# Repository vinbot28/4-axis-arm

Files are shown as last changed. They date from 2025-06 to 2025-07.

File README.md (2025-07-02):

# 4 Axis Arm
The **4 Axis Arm** is exactly what you think it is. Using 4 servos, the robotic arm achieves 4 degree of freedom movement through the: turret base, shoulder, elbow, and wrist rotation joints. All of the 3d printed parts are designed to use zero to no supports, and there are very few parts in the whole assembly. I've also created an electronics box containing potentiometers, an Arduino Nano (for its popularity and accessibility), and a custom PCB to greatly decrease the wiring hassle. 

Screenshot 2025-06-30 at 8 35 14 AM

Screenshot 2025-06-30 at 8 35 14 AM

Screenshot 2025-06-30 at 8 35 14 AM\
The wiring diagram for the potentiometers to PCB.

I created this project after seeing so many 6 axis arms pop up all over YouTube. Wanting one of my own, I quickly realized how much the components costed and the complexity of the control systems. Despite that, I really wanted to design and play with a robotic arm, and hence the decision to make a 4 axis. Additionally, I couldn't pass down the opportunity to CAD and design a PCB...

# General Instructions:
## Wiring: 
The PCB Silkscreen includes labels for which ports correspond to what component. Px = potentiometer; Sx = servo.\
Potentiometers:
- Pot 1      -> P1 (pcb) = Pin 19 (arduino)
- Pot 2      -> P2 (pcb) = Pin 20 (arduino) 
- Pot 3      -> P3 (pcb) = Pin 21 (arduino)
- Pot 4      -> P4 (pcb) = Pin 22 (arduino)
- Pot 5/claw -> P5 (pcb) = Pin 23 (arduino)

Servos:
- Servo 1/turret   -> S1 (pcb) = Pin 6 (arduino)
- Servo 2/shoulder -> S2 (pcb) = Pin 8 (arduino)
- Servo 3/elbow    -> S3 (pcb) = Pin 9 (arduino)
- Servo 4/wrist    -> S4 (pcb) = Pin 12 (arduino)
- Servo 5/effector -> S5 (pcb) = Pin 14 (arduino)

## Programming:
A sample program is included in this repository to control the servos using the potentiometers. Feel free to create your own programs to run pre-programmed movements, serial-based control, and much more!

# Bill of Materials:

| Item name | Amount Needed | Packs to buy | Total Cost | Link |
|---|---|---|---|---|
| MG946R Servo | 4 | 4 | 14.52 | https://www.aliexpress.us/item/3256806315358281.html |
| M4 6x5 Heat set | 23 | 1 | 2.64 | https://www.aliexpress.us/item/3256803396040989.html |
| M3 3x5 Heat set | 3 | 1 | 2.05 | https://www.aliexpress.us/item/3256803396040989.html |
| M4-6 SHCS | 20 | 1 | 1.55 | https://www.aliexpress.us/item/2255800598515019.html |
| M4-8 SHCS | 3 | 1 | 1.64 | https://www.aliexpress.us/item/2255800598515019.html |
| M3-6 SHCS | 3 | 1 | 1.41 | https://www.aliexpress.us/item/2255800598515019.html |
| Male/Female headers | 1 | 1 | 2.21 | https://www.aliexpress.us/item/2255800687544049.html |
| Female DC barrel jack | 1 | 1 | 1.53 | https://www.aliexpress.us/item/3256802343987191.html |
| Arduino nano | | 1 | 5.73 | https://www.aliexpress.us/item/3256806718205824.html |
| PCB | | 1 | 5 | jlcpcb.com |
| | | | | |
| 5v AC-DC Power supply | 1 | 1 | 9.99 | https://a.co/d/4vrQsQI |
| | | | | |
| | | Subtotal: | 48.27 | |
| | | Grand Total | 58.31 | |
| JLC Shipping | Aliexpress Shipping | Amazon Shipping | | |
| 3.2 | 6.84 | N/A | | |

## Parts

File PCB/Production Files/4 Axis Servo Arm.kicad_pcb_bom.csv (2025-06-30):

Designator | Quantity | Value | Footprint | Package | MPN | DNP | Mount_Type | Description
A1 | 1 | Arduino_Nano_v3.x | Arduino_Nano |  |  |  | tht | Arduino Nano v3.x
J1 | 1 | 5V DC BARREL | BarrelJack_Horizontal |  |  |  | tht | DC Barrel Jack with an internal switch
P1 | 1 | Pot_1 | PinHeader_1x03_P2.54mm_Vertical |  |  |  | tht | Generic connector, single row, 01x03, script generated (kicad-library-utils/schlib/autogen/connector/)
P2 | 1 | Pot_2 | PinHeader_1x03_P2.54mm_Vertical |  |  |  | tht | Generic connector, single row, 01x03, script generated (kicad-library-utils/schlib/autogen/connector/)
P3 | 1 | Pot_3 | PinHeader_1x03_P2.54mm_Vertical |  |  |  | tht | Generic connector, single row, 01x03, script generated (kicad-library-utils/schlib/autogen/connector/)
P4 | 1 | Pot_4 | PinHeader_1x03_P2.54mm_Vertical |  |  |  | tht | Generic connector, single row, 01x03, script generated (kicad-library-utils/schlib/autogen/connector/)
P5 | 1 | Pot_Claw | PinHeader_1x03_P2.54mm_Vertical |  |  |  | tht | Generic connector, single row, 01x03, script generated (kicad-library-utils/schlib/autogen/connector/)
S1 | 1 | Axis 1 | PinHeader_1x03_P2.54mm_Vertical |  |  |  | tht | Generic connector, single row, 01x03, script generated (kicad-library-utils/schlib/autogen/connector/)
S2 | 1 | Axis 2 | PinHeader_1x03_P2.54mm_Vertical |  |  |  | tht | Generic connector, single row, 01x03, script generated (kicad-library-utils/schlib/autogen/connector/)
S3 | 1 | Axis 3 | PinHeader_1x03_P2.54mm_Vertical |  |  |  | tht | Generic connector, single row, 01x03, script generated (kicad-library-utils/schlib/autogen/connector/)
S4 | 1 | Axis 4 | PinHeader_1x03_P2.54mm_Vertical |  |  |  | tht | Generic connector, single row, 01x03, script generated (kicad-library-utils/schlib/autogen/connector/)
S5 | 1 | Claw | PinHeader_1x03_P2.54mm_Vertical |  |  |  | tht | Generic connector, single row, 01x03, script generated (kicad-library-utils/schlib/autogen/connector/)

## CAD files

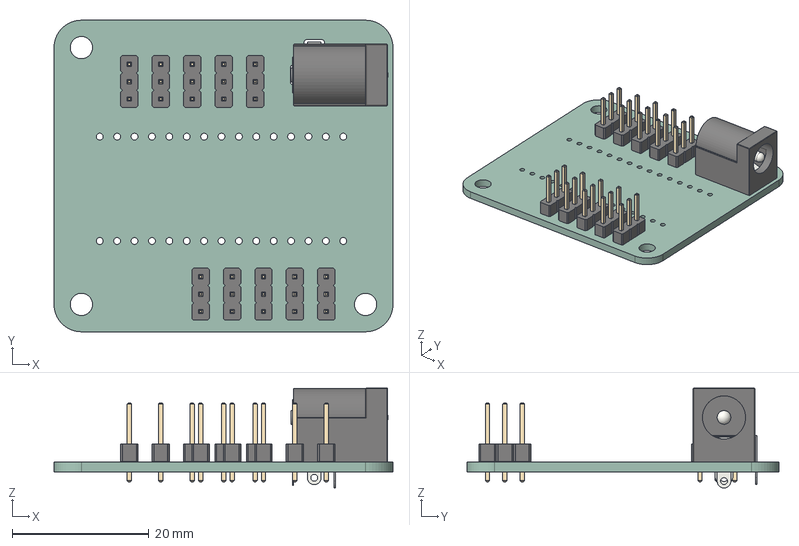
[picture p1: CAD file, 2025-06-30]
PCB/KiCad Files/4 Axis Servo Arm.step
49.5 x 45.5 x 14.6 mm
PinHeader_1x03_P2.54mm_Vertical x 10
BarrelJack_Horizontal
4 Axis Servo Arm_PCB

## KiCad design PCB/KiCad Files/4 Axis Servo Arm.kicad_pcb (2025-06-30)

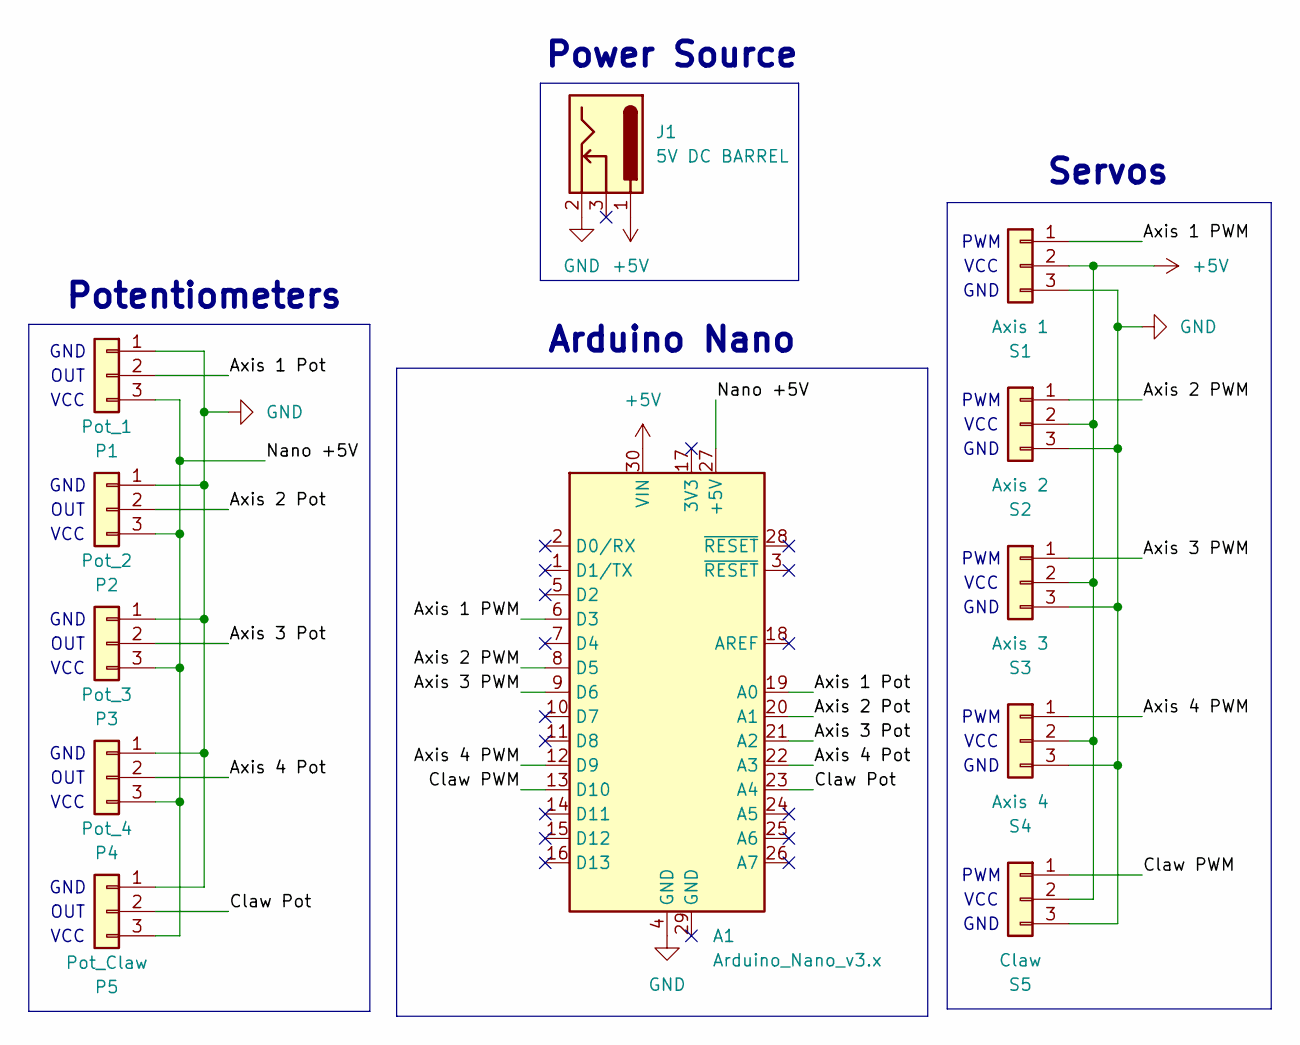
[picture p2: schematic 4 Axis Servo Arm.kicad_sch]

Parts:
A1: Arduino_Nano_v3.x; Arduino_Nano
J1: 5V DC BARREL; BarrelJack_Horizontal
P1: Pot_1; PinHeader_1x03_P2.54mm_Vertical
P2: Pot_2; PinHeader_1x03_P2.54mm_Vertical
P3: Pot_3; PinHeader_1x03_P2.54mm_Vertical
P4: Pot_4; PinHeader_1x03_P2.54mm_Vertical
P5: Pot_Claw; PinHeader_1x03_P2.54mm_Vertical
S1: Axis 1; PinHeader_1x03_P2.54mm_Vertical
S2: Axis 2; PinHeader_1x03_P2.54mm_Vertical
S3: Axis 3; PinHeader_1x03_P2.54mm_Vertical
S4: Axis 4; PinHeader_1x03_P2.54mm_Vertical
S5: Claw; PinHeader_1x03_P2.54mm_Vertical

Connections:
+5V: A1.30 (VIN), J1.1, S1.2, S2.2, S3.2, S4.2, S5.2
/Axis 1 PWM: A1.6 (D3), S1.1
/Axis 1 Pot: A1.19 (A0), P1.2
/Axis 2 PWM: A1.8 (D5), S2.1
/Axis 2 Pot: A1.20 (A1), P2.2
/Axis 3 PWM: A1.9 (D6), S3.1
/Axis 3 Pot: A1.21 (A2), P3.2
/Axis 4 PWM: A1.12 (D9), S4.1
/Axis 4 Pot: A1.22 (A3), P4.2
/Claw PWM: A1.13 (D10), S5.1
/Claw Pot: A1.23 (A4), P5.2
/Nano +5V: A1.27 (+5V), P1.3, P2.3, P3.3, P4.3, P5.3
GND: A1.4 (GND), J1.2, P1.1, P2.1, P3.1, P4.1, P5.1, S1.3, S2.3, S3.3, S4.3, S5.3

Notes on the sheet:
GND
PWM
VCC
GND
Servos
Potentiometers
Power Source
OUT
Arduino Nano

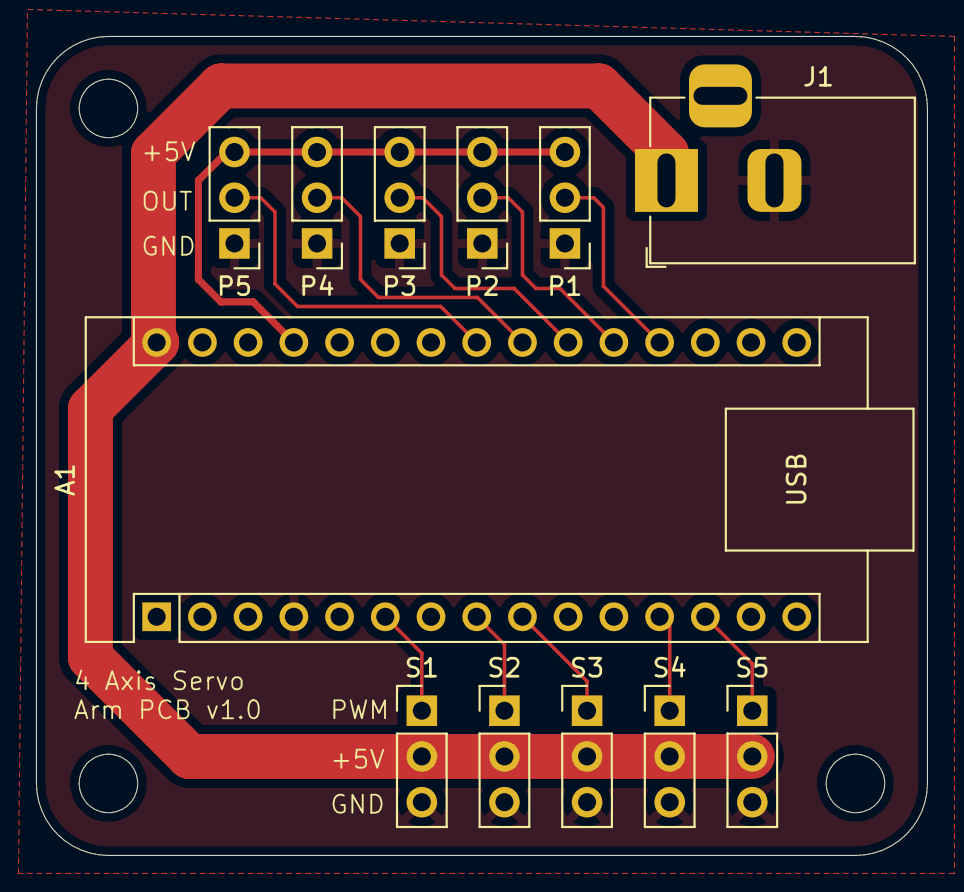
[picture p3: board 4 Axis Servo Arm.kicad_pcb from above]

Board: 2 copper layers, 49.5 x 45.5 mm, 12 parts (0 on the bottom side), 13 nets.

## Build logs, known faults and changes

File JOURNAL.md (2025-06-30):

---
title: 4 Axis Arm
author: Vincent
description: A robotic arm driven by servos and an Arduino.
created_at: 2025-06-18
---
## ***16.5 Total Hours***

# June 18th: Figured out the layout of the arm + got the base sorted out

Started cad work of the 4 axis. Also decided on using MG946R servos for their torque.

Axes: 
1. turret base
2. shoulder
3. elbow
4. wrist roll

CHALLENGE for this project: design all the 3d printed parts to not require slicer generated supports
* quite tedious to remove and it'd be a cool skill to have, especially since I do robotics and use 3d printing a lot

Single part base, printed upside down. Servo slots in from the bottom, and screws into some heat set inserts 
Assembly 2

Whole part is printed upside down, not requiring supports. To tackle the base mounting point overhangs, I added small bridges under to the counterbore. Much easier to understand in the photo, but it lets the printer have some material to print on top off.
I also chamfered the overhanging protrusion of the "legs" since printers don't struggle with printing at 45 degrees.
Assembly 2 (1)
Assembly 2 (2)

I'm currently doubting whether or not my servo cad file is correct in its dimensions, though it shouldn't be too bad to adjust them when I get the arm fabricated.

**Session Time: 3h**

# June 20: Shoulder axis (Axis 2)

Spent 30 minutes trying to decide how to continue the turret top without making it look so ugly. 
Settled on making the turret platform diameter from 90mm to 74mm. Also, chopping off unnecessary volume. Unfortunately, without splitting the part into two pieces, supports are needed for the shoulder servo recess. Maybe adjusting the goal to use supports only if they're fast and easy to remove?

Actually no I will just remove the bridged material since it's a waste of filament and space. Might also cause clearance issues when the arm is added later on:

Screenshot 2025-06-20 at 6 21 20 PM

I'm not going to lie, this (lack of) housing around the servo doesn't look too good. Thinking of having a cover plate but I don't want to increase complexity...\
Screenshot 2025-06-20 at 7 29 39 PM

Progress after ~2h of messing around:\
Axes 1 and 2 are completed! I added hardware models too, to make stuff look better. Moving on to designing the arm.\
Screenshot 2025-06-20 at 7 27 07 PM

Almost forget these cutouts for the servo mounting tabs.\
Screenshot 2025-06-20 at 9 55 33 PM

No clue how to make things look nice...it seems I can only tell if something's off. Especially in the case of the arm shape design.\
Screenshot 2025-06-20 at 8 07 26 PM

Made the arm shape look a bit nicer, + the 3rd axis servo mounting, but the arm looks too 2d.\
Screenshot 2025-06-20 at 10 23 25 PM

New issue: everything seems so skewed to the left, but my sketch for the turret base has so many lines that I can't tell what to change. Trying to move the shoulder servo closer to the center. Got it fixed though (second image). Everything is more centered and the forearm won't be too far from the center.\
Unfortunately, to stop the shoulder joint from being too cantilevered, I had to inset the surface where the shoulder servo horn connected to the arm. Hopefully supports are fine there.\
Screenshot 2025-06-20 at 11 18 13 PM
Screenshot 2025-06-20 at 11 24 43 PM

Attempted to beautify the arm. There's not much I can do to make it look nice besides spam chamfers and fillets, so that's what I did. Personally I think it looks pretty good, but it definitely still looks out of place. Good enough?
Screenshot 2025-06-20 at 11 45 23 PM

For tomorrow, should probably clean this plate up. Looks out of place.
Screenshot 2025-06-20 at 11 42 56 PM

End of day progress: Pretty good, accomplished axes 2 and started 3.\
Screenshot 2025-06-20 at 11 47 08 PM

**Session Time: 4.5h**

# June 21: Axis 3

Starting axis 3. Sketch for side view of axis 3 + axis 4 servo.\
Screenshot 2025-06-21 at 10 21 36 AM

Drew this up for the shape of the remaining axes:\
Screenshot 2025-06-21 at 10 24 27 AM

Finally something presentable for axis 3. Axis 4 will be inline with axis 3 point of rotation, and that defined many of the locational dimensions in the sketch. Also tried to include some curves so everything doesn't look to boring and simplistic.\
Screenshot 2025-06-21 at 12 00 22 PM

YES! No clearance issues today, and the proportions seem about right. Time to make the actual servo mount part.\
Screenshot 2025-06-21 at 12 07 20 PM

Finished servo mount. I'm not too sure if the actual mounting towers would break. With the (non) loads this arm will tackle, I have my doubts they'll break. It's also a 9.9mm^2 tower so I could just increase walls + infill as needed.\
Screenshot 2025-06-21 at 1 15 51 PM

I also took some time to recenter everything so that axis 4 is on the line of symmetry of the base:\
Screenshot 2025-06-21 at 1 19 06 PM
Screenshot 2025-06-21 at 1 19 16 PM

**Session Time. 2.5h**

# June 22: PCB TIME

Spent an hour trying to figure out what symbols and footprints to use for my components...and they're not even ICs. Had to watch some pcb tutorial videos to figure out what to use for 3 pin headers and the barrel jack. Attempted to connect the parts on the schematic, but it got messy quick.\


Learned of "labels?" which you can connect to and it bridges between connections to the same label. Made the schematic sooooo clean.\


I used the net checker tool to verify my connections went to the right spots. However, ERC gave me an error about output pins not going into input pins, or something like that. Some googling told me it's just a thing with the input/output power settings for the components. Also, I know that the connections are fine so I just ignored the error. MOVING ON TO PCB LAYOUT!!!

I organized the pin headers by servo or potentiometer, and put it on the respective sides of the nano where the connections didn't overlap each other. I may have redone the layout 3 times...anyway I learned to do a ground pour for the GND lines so I didn't have to route those traces. Yay! Thinking I was done, I ran the DRC, which gave me a "thermal relief connection to zone incomplete" error. Turns out my ground pour wasn't able to reach one of the ground pins on the nano. That was easy to fix just by moving my 5v line out of the way. And now, I have a PCB! I'll work on the silkscreen tomorrow.\



**Session Time. 3.5h**

# June 23

Finished the PCB. I added 3.25mm mounting holes, as well as some silkscreen labels. DRC checks were all good!\



Since the PCB was smooth sailing, I'm going to add an enclosure to this pcb. There needs to be something holding the potentiometers and protecting the board. Exported pcb as a .step from kicad.
Successfully imported it into onshape. I also added a nano model:\


Ended the day with figuring out the layout for the potentiometers and started the frame model. Going to use m3 heat sets to secure pcb, and m4 heat sets for the cover. 


**Session Time. 1.0h**

# June 29

Finished the electronics case. Adjusted the potentiometers to not block the servo ports. Good thing there's only 5 pots. 



I checked online for the usb and dc jack cable sizes, to make sure there's enough space for wire clearance:



Overall looks pretty good. Labeled the pots for the joints they would control. Seems like we're done!


** Session Time: 2.0h **

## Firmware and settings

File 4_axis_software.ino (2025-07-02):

#include <Servo.h>

// effector code has been commented out in case user wants to use expansion slot

// declaring servos
Servo turret;
Servo shoulder;
Servo elbow;
Servo wrist;
// Servo effector; 

// assigning pins to servos (pwm ports)
const int turretPin = 6;
const int shoulderPin = 8;
const int elbowPin = 9;
const int wristPin = 12;
// const int effectorPin = 14; 

// assigning pins to potentiometers (analog ports)
const int T_potPin = 19;
const int S_potPin = 20;
const int E_potPin = 21;
const int W_potPin = 22;
//const int EF_potPin = 23;

// vars for pot readings
int T_potVal;
int S_potVal;
int E_potVal;
int W_potVal;
//int EF_potVal;

void setup() {
  turret.attach(turretPin);
  shoulder.attach(shoulderPin);
  elbow.attach(elbowPin);
  wrist.attach(wristPin);
  //effector.attach(effectorPin);
}

void loop() {
  //grabbing values from pots
  T_potVal = analogRead(T_potPin);
  S_potVal = analogRead(S_potPin);
  E_potVal = analogRead(E_potPin);
  W_potVal = analogRead(W_potPin);
  //EF_potVal = analogRead(EF_potPin);

  //scaling pot values to servo 0-180 value
  T_potVal = map(T_potVal, 0, 1023, 0, 180);
  S_potVal = map(S_potVal, 0, 1023, 0, 180);
  E_potVal = map(E_potVal, 0, 1023, 0, 180);
  W_potVal = map(W_potVal, 0, 1023, 0, 180);
  //EF_potVal = map(EF_potVal, 0, 1023, 0, 180);

  //sending values to servo
  turret.write(T_potVal);
  shoulder.write(S_potVal);
  elbow.write(E_potVal);
  wrist.write(W_potVal);
  //effector.write(EF_potVal);
  
  delay(20);
}

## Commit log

2025-06-30 added production files
    [4 Axis Servo Arm.kicad_pcb_bom.csv, 4 Axis Servo Arm.kicad_pcb_positions.csv]
2025-06-30 updating stuff
    [4 Axis Servo Arm.kicad_pcb_bom.csv, 4 Axis Servo Arm.kicad_pcb_positions.csv]
2025-06-30 kicad files
    [4 Axis Servo Arm.kicad_pcb, 4 Axis Servo Arm.kicad_sch, 4 Axis Servo Arm.step]
2025-06-30 added kicad files and renamed folders
    [4 Axis Servo Arm.kicad_pcb, 4 Axis Servo Arm.kicad_pcb_bom.csv, 4 Axis Servo Arm.kicad_pcb_positions.csv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]
2025-07-01 Update 4 axis bom.csv
    [4 axis bom.csv]
